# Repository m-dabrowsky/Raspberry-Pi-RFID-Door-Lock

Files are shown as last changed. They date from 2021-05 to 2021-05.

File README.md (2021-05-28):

# Zamek RFID

Projekt opiera się na Raspberry Pi 4 i umożliwia otwieranie oraz zamykanie szafki za pomocą odpowiedniego identyfikatora w postaci karty lub breloczka RFID. 

Po przyłożeniu identyfikatora do czytnika RC-522 następuje odczytanie tokenów i przekazanie ich do RPI. W przypadku zgodności wprowadzonego w programie identyfikatora z numerem zbliżanej karty lub breloczka program wita się z właścicielem karty poprzez wyświetlenie na wyświetlaczu LCD np: `Welcome, Michal!`. Dodatkowo zapala się zielona dioda, która wraz z tekstem: `Access granted`, informuje o uzyskaniu dostępu. W tym momencie następuje ruch serva z pozycji 0 do pozycji 180 stopni powodując otwarcie zasuwki meblowej. 

W celu ponownego zamknięcia szafki należy ponownie przyłożyć odpowiedni token do czytnika, po czym nastąpi dwukrotne zapalanie i zgaszenie zielonej diody oraz wyświetlenie komunikatu: `Closing the lock`. Po zgaszeniu diod, serwo wraca do pozycji 0, a na wyświetlaczu pojawia się informacja o zamknięciu szafki: `Locked`.

Przyłożenie do czytnika karty z nieprawidłowym identyfikatora spowoduje zapalenie czerwonej diody oraz wyświetlenie informacji: `Invalid card`.

## Potrzebne elementy

1. Raspberry Pi 4
2. Wyświetlacz LCD 16x2
3. Czytnik RFID RC-522
4. Potencjometr 10k Ohm
5. Servo 9G
6. Dioda LED czerwona i zielona
7. Rezystor 330 Ohm x2

## Przygotowanie Raspberry PI

Do wykonania projektu będzie potrzebnych kilka bibliotek. W pierwszej kolejności należy wykonać aktualizacje RPI:

```bash
sudo apt-get update 
sudo apt-get upgrade
```

1. Instalacja Raspberry Pi GPIO Python Library - potrzebna do obsługi pinów GPIO oraz sterowania PWM:

```bash
sudo pip3 install RPi.GPIO
```

2. Instalacja RPLCD Library - potrzebna do wyświetlacza LCD i jego konfiguracji:

```bash
sudo pip3 install RPLCD
```

3. Instalacja MFRC422 Library - komunikacja z czytnikiem RFID:

Moduł czytnika RFID wykorzystuje interfejs SPI. W związku z tym należy się upewnić czy RPI ma aktywowany ten interfejs:

```bash
sudo raspi-config
```

Po wyświetleniu okna konfiguracyjnego z opcjami, należy przejść do "**5 Interfacing Options**", a następnie wybrać "**P4 SPI**" zatwierdzając enterem, oraz na pytanie o włączenie interfejsu SPI odpowiedzieć **Yes**.

Zanim SPI będzie całkowicie włączony należy zrestartować Raspberry:

```bash
sudo reboot
```

Jeśli po wpisaniu w konsolę `lsmod | grep spi` wyświetli się “**spi_bcm2835**” oznacza to że wszystko jest gotowe do dalszej pracy.

Do zainstalowania została jeszcze biblioteka odpowiedzialna za komunikacje z czytnikiem.

```bash
sudo pip3 install spidev
sudo pip3 install mfrc522
```

## Schemat połączenia
<div class="container">
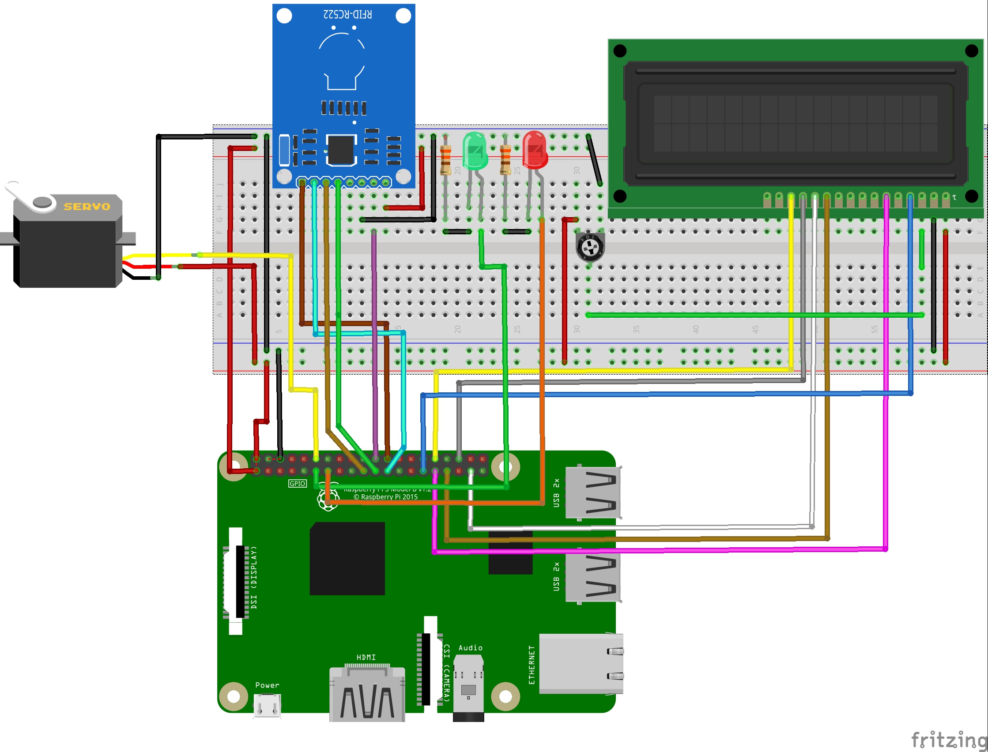
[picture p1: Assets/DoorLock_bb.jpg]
    
</div>

!!! Na schemacie wdarł się błąd - Vss i Vdd wyświetlacza zostały ze sobą zamienione !!!
### Tabela połączeń

| RFID RC-522 | Raspberry Pi 4 |
| --- | --- |
| Vcc (3,3V) | 3,3V (fizyczny pin 1) |
| RST | GPIO 25 |
| GND | GND |
| RQ | - |
| MISO | GPIO 9 |
| MOSI | GPIO 10 |
| SCK | GPIO 11 |
| SDA | GPIO 8 |
| **LCD 16x2**  | |
| Vss | GND |
| Vdd | 5V (fizyczny pin 2) |
| V0 | środkowa nóżka potencjometru |
| RS | GPIO 5 |
| RW | - |
| E | GPIO 6 |
| D0,D1,D2,D3 | |
| D4 | GPIO 13 |
| D5 | GPIO 26 |
| D6 | GPIO 16 |
| D7 | GPIO 12 |
| A,K | - |
| **Servo 9G**  | |
| Vcc | 5V |
| GND | GND |
| Data | GPIO 18 (PWM) |
| **LED_GREEN** | GPIO 17 |
| **LED_RED** | GPIO 27 |

## Sterowanie PWM

Położenie ramienia serwa zmienia się, podając odpowiedzi sygnał PWM. W zależności od parametrów sygnału, serwo może obracać w lewo/prawo, ustawić w jedną ze skrajnych pozycji (0 i 180 stopni), w pozycję neutralną (90 stopni) lub po prostu obrócić się o 360 stopni.  

<div class="container">
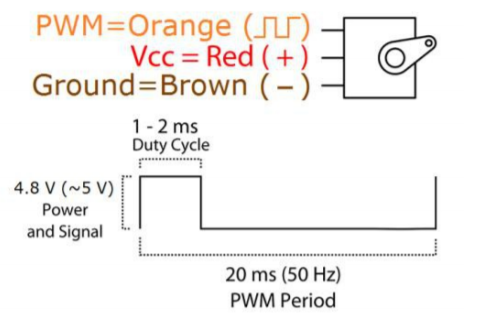
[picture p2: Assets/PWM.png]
    
</div>

Serwo oczekuje sygnału PWM o częstotliwości 50 Hz (cykl o długości 20 ms). Układ sterujący próbkuje długość stanu wysokiego. Może ona przyjmować charakterystyczne wartości które układ sterujący zinterpretuje jako: 

- 0,6 ms - ustaw serwo w pozycji skrajnej 0
- 1,5 ms - ustaw serwo w pozycji neutralnej (90 stopni)
- 2,5 ms - ustaw serwo w pozycji skrajnej 180 stopni

Podstawiając powyższe czasy do wzoru: wypelnienie = \frac{t [ms]* 100}{20[ms]}, otrzymano odpowiednio wypełnienia: 3%, 7,5%, 12,5%.

## Kod programu

Aby korzystać z oznaczeń pinów jako GPIO, a nie ich fizycznej numeracji ustawiono tryb na BCM:

```python
GPIO.setmode(GPIO.BCM) 
```

W projekcie oprócz wyświetlacza LCD wykorzystano LEDy do informowania o poprawnym lub błędnym ID. Zieloną i czerwoną diodę podłączono odpowiednio do pinów GPIO 17 i GPIO 27. Dodatkowo sygnał z serwa podłączono pod GPIO 18 który jest pinem PWM.

```python
# --- definicja pinów wyjściowych ---
PWM_PIN = 18                                      
GREEN_LED = 17                                      
RED_LED = 27 

# --- definicja kanałów jako wyjścia ---
GPIO.setup(RED_LED,GPIO.OUT)
GPIO.setup(GREEN_LED,GPIO.OUT)
GPIO.setup(PWM_PIN, GPIO.OUT)  
```

Poniżej określono stałe wartości takie jak częstotliwość pracy PWM oraz prawidłowe ID karty, które umożliwi otworzenie drzwi.

```python
freq = 50                                           # częstotliowść przebiegu PWM
correctID = 387886317638                            # Prawidłowe ID
count = 0
```

`count` służy do zliczania liczby przyłożonej karty.

#### Wyświetlacz

Dzięki bibliotece RPLCD można bardzo łatwo skonfigurować podłączany wyświetlacz LCD.

```python
# Konfiguracja wyświetlacza LCD
lcd = CharLCD(numbering_mode=GPIO.BCM, pin_rs=5, pin_e=6, pins_data=[13, 26, 16, 12], cols=16, rows=2, dotsize=8, charmap='A02', auto_linebreaks=False)
```

`numbering_mode` określa konwencje oznaczeń pinów, a następnie do każdego pinu w wyświetlaczu przypisywane są odpowiednie numery pinów na płytce RPI. 

Wyświetlacz wykorzystany w projekcie ma 2 wiersze i możliwość zapisania 16 znaków w każdym z nich. Dlatego `cols` i `rows` przyjmują takie wartości. 

`charmap` odpowiada za wyświetlanie znaków. Domyślnie jest to wartość A02, jednak w przypadku niepoprawnego wyświetlania niektórych znaków należy zmienić na A00.

`auto_linebreaks` jest to automatyczny podział wierszy. Jeśli tekst nie będzie mieścił się w 16 znakach, to zostanie automatycznie przeniesiony do kolejnego wiersza.

#### Odczyt ID z karty

Odczyt danych z karty odbywa się za pomocą biblioteki mfrc522

```python
id = reader.read()
```

#### Przyłożono poprawną kartę 

W programie sprawdzany jest warunek czy ID zbliżonej karty jest równej prawidłowemu ID zdefiniowanemu na początku kodu.

Jeśli warunek zostanie spełniony następuje zwiększenie licznika zbliżeń karty o jeden 					`count = count + 1` , a następnie wykonanie poniższego kodu:

```python
  lcd.clear()                             # Czyszczenie ekranu
  lcd.write_string('Hello Michal!')       # Wyświetlenie przywitania
  sleep(1)                                # Czekanie 1s
  lcd.clear()                             # Czyszczenie ekranu
  lcd.write_string("Access granted")      # Wyświetlenie informacji o przyznanym dostępie
  GPIO.output(GREEN_LED, GPIO.HIGH)       # Zapalenie GREEN_LED

  pwm.ChangeDutyCycle(12.5)               # Zmiana wypełnienia sygnału PWM (180 stopni)
  sleep(1)                                # Czekanie 1s
  lcd.clear()                             # Czyszczenie ekranu
  GPIO.output(GREEN_LED, GPIO.LOW)        # Zgaszenie GREEN_LED
  sleep(0.5)      
```

Prawidłowe ID powoduje przywitanie właściciela karty oraz poinformowanie o przyznanym dostępie. Dalej zostaje zapalona zielona dioda oraz ruch serwa do pozycji skrajnej 180 stopni, co powoduje otworzenie zamka.

W celu ponownego zamknięcia zamka, należy jeszcze raz przyłożyć kartę do czytnika po czym licznik zbliżeń osiągnie wartość równą dwa co spowoduje wykonanie poniższego kodu:

```python
lcd.clear()                             # Czyszczenie ekranu
lcd.write_string("Closing the")         # Wyświetlenie informacji o zamykaniu zamka 				w pierwszym wierszu
lcd.cursor_pos = (1, 0)                 # Przejście do drugiego wiersza
lcd.write_string('lock')
for i in range(2):                      # Pętla odpowiedzialna za 2-krotne zapalenie i zgaszenie GREEN_LED
    GPIO.output(GREEN_LED, GPIO.LOW)
    sleep(1)
    GPIO.output(GREEN_LED, GPIO.HIGH)
    sleep(1)
    GPIO.output(GREEN_LED, GPIO.LOW)
pwm.ChangeDutyCycle(3)                  # zmiana wypełnienia sygnału PWM (0 stopni)
lcd.write_string("Locked")              # Wyświetlenie informacji o zamyknięciu zamka
lcd.clear()                             # Czyszczenie ekranu
count = 0                               # Wyzerowanie licznika
sleep(0.5)                              # Czekanie 0.5s
```

Użytkownik zostaje poinformowany o zamykaniu zamka i następuje dwu krotne odliczanie za pomocą zielonej diody która się zapali i zgaśnie po czym serwo zmieni swoja pozycję na 0 stopni. Te działanie zostanie zakończone informacją potwierdzającą zamknięcie zamka. 

<div class="container">
    
</div>

#### Przyłożono niepoprawną kartę

```python
 lcd.clear()                                 # Czyszczenie ekranu
 lcd.write_string("Invalid card")            # Wyświetlenie informacji o błędnej karcie dostępu
 GPIO.output(RED_LED,GPIO.HIGH)              # Zapalenie RED_LED
 sleep(1)                                    # Czekanie 1s
 lcd.clear()                                 # Czyszczenie ekranu
 GPIO.output(RED_LED,GPIO.LOW)               # Zgaszenie RED_LED
```

Przyłożenie nieprawidłowej karty spowoduje poinformowanie o tym fakcie za pomocą czerwonej diody oraz wiadomości: `Invalid card`

<div class="container">
    
</div>

## Dalszy rozwój projektu

Niestety servo nie posiada wystarczającej mocy aby otwierać/zamykać duże i mocne zamki. Więc aby to osiągnąć należałoby wykorzystać elektromagnes lub większy silnik połączony z przekaźnikiem. A jakakolwiek próba wejścia z nieprawidłowym ID może spowodować wysłanie informacji na mail lub telefon. 

W przypadku większej ilości osób które miałby dostęp do pomieszczenia/szafki należałoby stworzyć baze danych do przechowywania identyfikatorów i ich właścicieli. 

Dodatkowo projekt może zostać wykorzystany nie tylko do otwierania/zamykania zamka, ale również chociażby do odsłaniania rolet, czy włączania różnych urządzeń.

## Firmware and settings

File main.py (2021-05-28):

import RPi.GPIO as GPIO                             # Obsługa pinów GPIO i PWM
from time import sleep                              # Biblioteka do wykorzystania funkcji sleep()
from mfrc522 import SimpleMFRC522                   # Biblioteka obsługi czytnika RFID
from RPLCD.gpio import CharLCD                      # Obsługa wyświetlacza LCD

GPIO.setwarnings(False)                             # wyłączenie ostrzeżeń podczas pracy kodu
"""-----------------------------------------"""
GPIO.setmode(GPIO.BCM)                              # konfiguracja konwencji oznaczenia pinów GPIO

# --- definicja pinów wyjściowych ---
PWM_PIN = 18                                        # Sygnał PWM ma być wygenerowany na GPIO18, czyli fizyczny pin 12
GREEN_LED = 17                                      # Dioda zielona informująca o poprawnym ID
RED_LED = 27                                        # Dioda czerwona informująca o błędnym ID

# --- definicja kanałów jako wyjścia ---
GPIO.setup(RED_LED,GPIO.OUT)
GPIO.setup(GREEN_LED,GPIO.OUT)
GPIO.setup(PWM_PIN, GPIO.OUT)  

freq = 50                                           # częstotliowść przebiegu PWM
correctID = 387886317638                            # Prawidłowe ID
count = 0

"""-----------------------------------------"""

reader = SimpleMFRC522()                            # Stworzenie instancji

# Konfiguracja wyświetlacza LCD
lcd = CharLCD(numbering_mode=GPIO.BCM, pin_rs=5, pin_e=6, pins_data=[13, 26, 16, 12],
              cols=16, rows=2, dotsize=8,
              charmap='A02',
              auto_linebreaks=False)


pwm = GPIO.PWM(PWM_PIN,freq)                        # definicja kanału PWM na pinie (18) i częstotliwości 50 Hz (20ms)

# Uruchomienie PWM: 3 oznacza wypełnienie 3% czyli pozycja 0
pwm.start(3)
GPIO.output(PWM_PIN, True)


while True:
    lcd.clear()                                     # Czyszczenie ekranu
    lcd.write_string('Put your ID card')            # Wyświetlenie informacji o zbliżeniu karty

    id, text = reader.read()                        # Odczyt ID z karty
        
    if(id == correctID):                            # jeśli przyłozona karta jest zgodna z ID

        count = count + 1                           # Zwiększenie licznika (po ponownym przyłożeniu karty)
        if(count == 2):                             # Jeśli drugi raz przyłoży się kartę następuje zamknięcie zamka
            lcd.clear()                             # Czyszczenie ekranu
            lcd.write_string("Closing the")         # Wyświetlenie informacji o zamykaniu zamka w pierwszym wierszu
            lcd.cursor_pos = (1, 0)                 # Przejście do drugiego wiersza
            lcd.write_string('lock')
            for i in range(2):                      # Pętla odpowiedzialna za 2-krotne zapalenie i zgaszenie GREEN_LED
                GPIO.output(GREEN_LED, GPIO.LOW)
                sleep(1)
                GPIO.output(GREEN_LED, GPIO.HIGH)
                sleep(1)
                GPIO.output(GREEN_LED, GPIO.LOW)
            pwm.ChangeDutyCycle(3)                  # zmiana wypełnienia sygnału PWM (0 stopni)
            lcd.write_string("Locked")              # Wyświetlenie informacji o zamyknięciu zamka
            lcd.clear()                             # Czyszczenie ekranu
            count = 0                               # Wyzerowanie licznika
            sleep(0.5)                              # Czekanie 0.5s
        else:
            lcd.clear()                             # Czyszczenie ekranu
            lcd.write_string('Hello Michal!')       # Wyświetlenie przywitania
            sleep(1)                                # Czekanie 1s
            lcd.clear()                             # Czyszczenie ekranu
            lcd.write_string("Access granted")      # Wyświetlenie informacji o przyznanym dostępie
            GPIO.output(GREEN_LED, GPIO.HIGH)       # Zapalenie GREEN_LED

            pwm.ChangeDutyCycle(12.5)               # Zmiana wypełnienia sygnału PWM (180 stopni)
            sleep(1)                                # Czekanie 1s
            lcd.clear()                             # Czyszczenie ekranu
            GPIO.output(GREEN_LED, GPIO.LOW)        # Zgaszenie GREEN_LED
            sleep(0.5)                              # Czekanie 0.5s


        

    else:

        lcd.clear()                                 # Czyszczenie ekranu
        lcd.write_string("Invalid card")            # Wyświetlenie informacji o błędnej karcie dostępu
        GPIO.output(RED_LED,GPIO.HIGH)              # Zapalenie RED_LED
        sleep(1)                                    # Czekanie 1s
        lcd.clear()                                 # Czyszczenie ekranu
        GPIO.output(RED_LED,GPIO.LOW)               # Zgaszenie RED_LED
pwm.stop()
GPIO.cleanup()                                      # wyłączenie wszystkich kanałów PWM
